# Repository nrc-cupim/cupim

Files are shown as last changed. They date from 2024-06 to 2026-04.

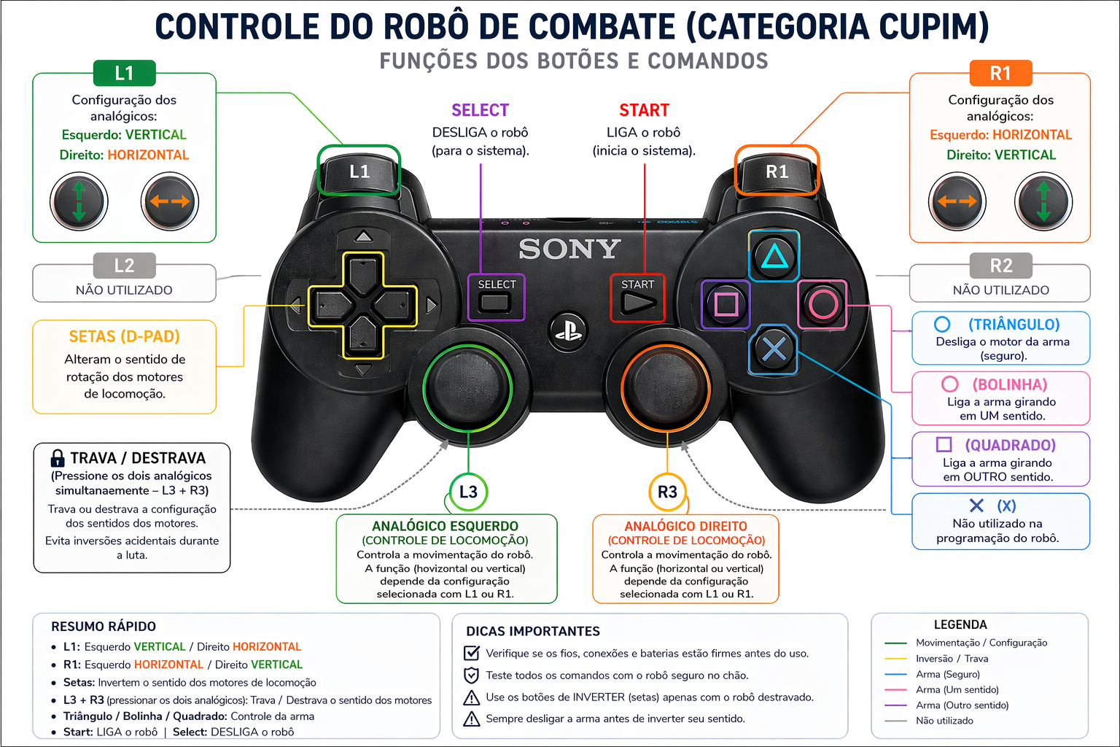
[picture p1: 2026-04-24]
Codigos/funcoes-controle.png

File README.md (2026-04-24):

# start\_Engenharia Automação e Elétrica

Materiais desenvolvidos para a atividade.

* Apostilas: contém documentação completa sobre a eletrônica (hardware) e a programação (firmware) do robô, além de tutoriais de instalação das ferramentas necessárias (drivers, softwares, bibliotecas, etc)
  
* Códigos: contém o código principal do robô, código para aplicar o filtro MAC do controle e código para descobrir os parâmetros de um controle
  
* Hardware: contém fotos da placa, arquivo para produção/prototipagem (GERBER) e os arquivos de projeto (abrir no software EasyEDA)
  
* Mecânica: contém arquivos dxf (para corte a laser) das peças da estrutura mecânica dos robôs desse ano e dos anos anteriores e modelos de rodas alternativas

----

## Regras

Para acessar as regras da categoria de cupim e os critérios de julgamento das lutas, clique [aqui](https://events.robocore.net/ironcup-2026/rules)

----

## Vídeos
* [IronCup 2026 - 10 Anos](https://www.youtube.com/watch?v=BdECDlp-MfM)
* [Finais start_Inatel 2025](https://www.youtube.com/watch?v=BfLkFSdPqyA)

----

## Links uteis

* [Biblioteca Bluepad32](https://bluepad32.readthedocs.io/en/latest/)
* [Tutorial filtro MAC do controle](https://bluepad32.readthedocs.io/en/latest/FAQ/#how-to-pair-just-one-controller-to-one-particular-board)
* [Driver ESP32](https://www.silabs.com/developers/usb-to-uart-bridge-vcp-drivers)
* [IDE Arduino](https://www.arduino.cc/en/software)
* [Onshape](https://www.onshape.com/en/)
* [EasyEDA](https://easyeda.com/pt)
* [Manual ponte H DRV8833](https://www.ti.com/lit/ds/symlink/drv8833.pdf?ts=1716022162879)

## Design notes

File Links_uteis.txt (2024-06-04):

Bilioteca controle:	https://bluepad32.readthedocs.io/en/latest/
			https://github.com/ricardoquesada/bluepad32

Tutorial filtro MAC controle: https://bluepad32.readthedocs.io/en/latest/FAQ/#how-to-pair-just-one-controller-to-one-particular-board

Driver ESP32: https://www.silabs.com/developers/usb-to-uart-bridge-vcp-drivers

Arduino: https://www.arduino.cc/en/software

OnShape: https://www.onshape.com/en/

Easy EDA: https://easyeda.com/pt

Datasheet ponte H: https://www.ti.com/lit/ds/symlink/drv8833.pdf?ts=1716022162879

Datasheet TIP 122: https://www.st.com/resource/en/datasheet/tip120.pdf

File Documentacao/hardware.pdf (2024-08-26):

# Guia de hardware

## Sumário

1 Componentes | 3
2 Esquema elétrico | 14

## 1 Componentes

### 1.1 Célula de bateria

Responsável por alimentar o robô, permitindo seu funcionamento. A bateria utilizada neste projeto é do tipo Li-ion 18650.

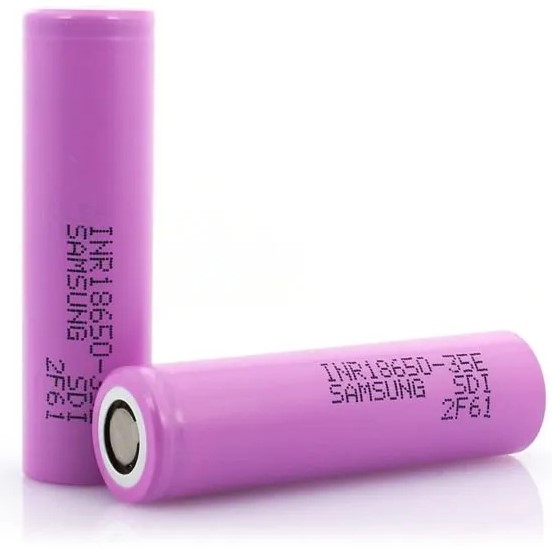
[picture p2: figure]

Figure 1: Célula de bateria 18650

- Capacidade: 2200mAh (quanto maior a capacidade, mais tempo a bateria irá durar);
- Polaridade: cada bateria possui um lado positivo e um lado negativo. O lado da bateria que possui um chanfro / corte / ressalto é o positivo. E possível ainda identificar a ´ polaridade utilizando um multímetro;
- Tensão Nominal: A tensão nominal de uma célula 18650 é de 3.7V, podendo variar entre 4.2V (quando completamente carregada) e 3.2V (quando descarregada).

E possível associar células de baterias em série (positivo de uma conectada no negativo de outra) ´ para produzir tensões maiores. Ao associá-las dessa forma, a tensão de saída será igual ao somatório das tensões de cada célula de bateria.

Existem modelos de baterias com diferentes capacidades, tamanhos, pesos e tipos de materiais. Existem ainda baterias que já vêm com várias células associadas (2s, 3s, ...).

### 1.2 Suporte de bateria

Componente utilizado para manter as baterias firmemente no lugar, garantindo uma conexão elétrica segura e estável entre as baterias e o circuito. Esse suporte permite a conexão de duas baterias Li-íon 18650 em série.

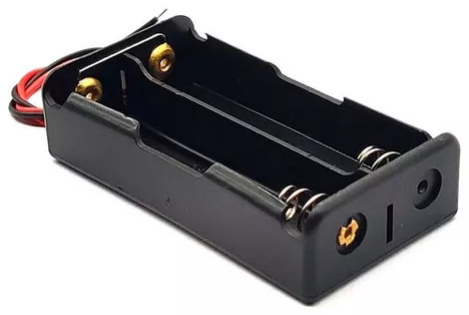
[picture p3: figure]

Figure 2: Suporte para 2 baterias 18650

- No interior do suporte há um desenho mostrando como cada bateria deve ser colocada;
- Polaridade da saída: o fio vermelho é o positivo (+) e o fio preto, o negativo (-).

### 1.3 Carregador de bateria

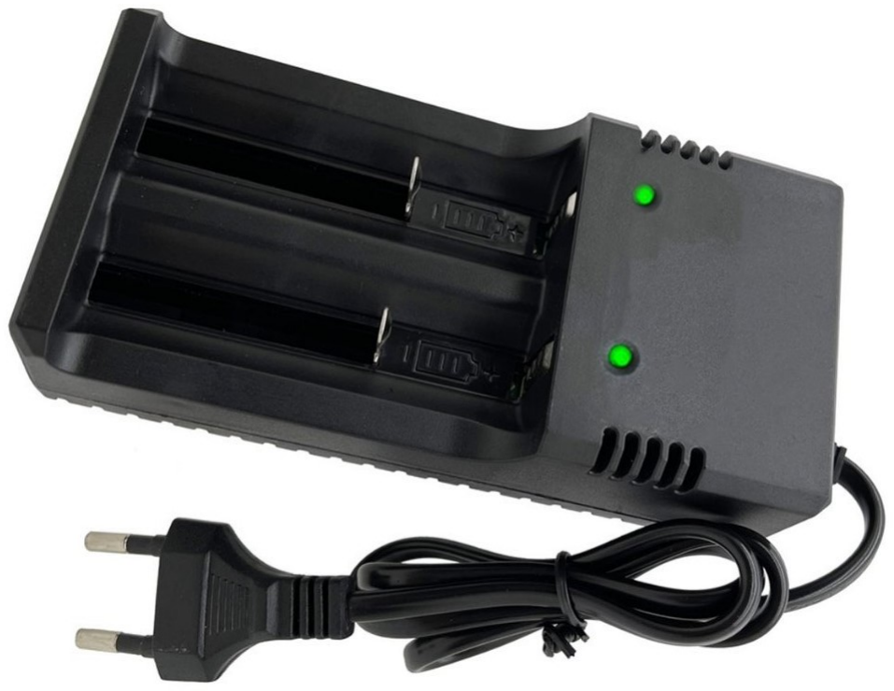
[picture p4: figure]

Figure 3: Carregador para duas baterias 18650

Para carregar a bateria, basta encaixa-la no interior do suporte, pressionando a parte metálica que fica no meio para baixo. O positivo da bateria deve ficar para cima (conector mais próximo ao led de indicação).

- Led vermelho: indica que a bateria não está completamente carregada;
- Led verde: indica que a bateria está completamente carregada.

Observação: é necessário conectar o carregador na tomada para que os leds indiquem corretamente o estado da bateria.

### 1.4 Regulador 7805

Utilizado para regular a tensão da bateria, que varia de 6,4 a 8,4 V, para 5 V. Essa regulagem é necessária para se fazer a alimentação da ESP32.

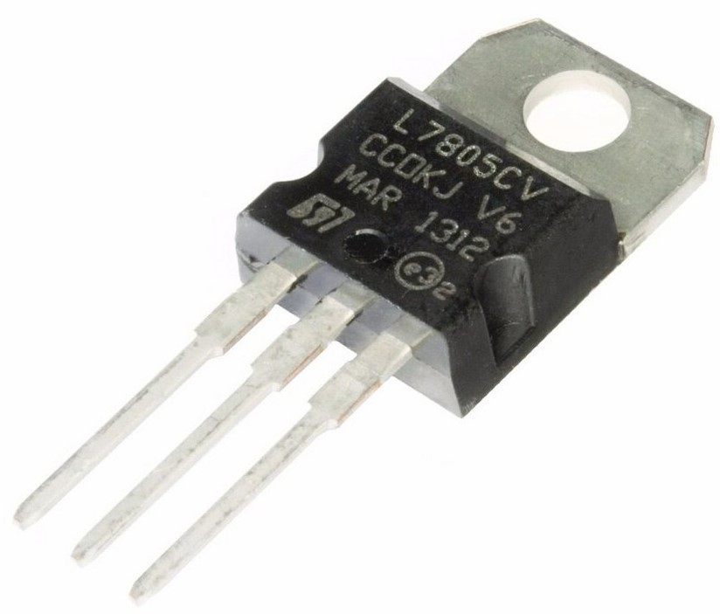
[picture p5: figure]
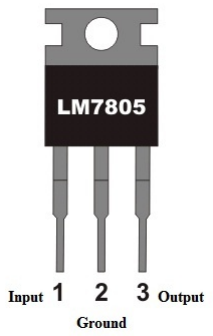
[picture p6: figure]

(a) (b)

Figure 4: Regulador 7805

- Pinagem: possui três terminais - entrada (Vin), terra (GND) e saída (Vout).
- Parâmetros elétricos:

– Tensão de entrada: 7,5 a 35V
– Tensão de saída: 5V
– Maxima corrente que o componente é capaz de fornecer na saída: 1A

Observações:

- Para mais informações do componente, consulte seu datasheet
- Caso a conexão dos pinos não seja feita da forma correta, o componente explode. Portanto, deve-se tomar muito cuidado ao fazer as conexões.
- E recomendado a utilização de um dissipador de calor para impedir que o componente ´ esquente muito. Entretanto, este não foi utilizado devido à limitação de espaço na placa.

### 1.5 ESP32 WROOM-32

Microcontrolador responsável por ler as informações do controle Bluetooth e atuar no controle dos motores. E o cérebro do robô. ´

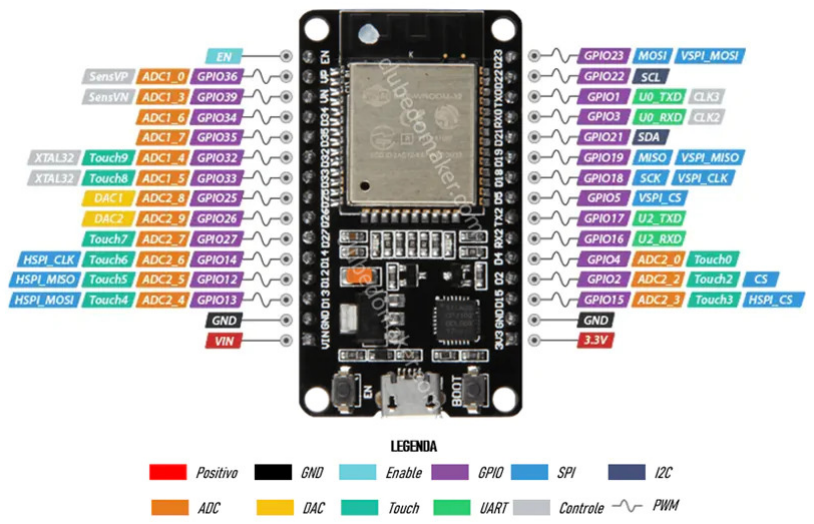
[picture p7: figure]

Figure 5: Pinagem ESP32 WROOM32 30 pinos

A alimentação da placa pode ser feita por meio do conector USB presente na placa ou então por meio do pino VIN. A tensão recebida no pino VIN deve ser de 5V. As opções de alimentação são mutuamente exclusivas, ou seja, nunca se deve alimentar a placa das duas maneiras simultaneamente. Se for alimentar pelo pino VIN, deve-se remover o cabo USB e vice-versa. No projeto desenvolvido, a tensão vinda da bateria é regulada para 5V e é encaminhada para o pino VIN da ESP.

O controlador trabalha em nível lógico 3,3V. Portanto, todo sinal de saída da placa poderá ter até 3,3V e todo sinal de entrada deve ter até 3,3V.

Do lado oposto ao conector USB fica a antena Bluetooth do microcontrolador. A fim de evitar problemas de conexão (queda de conexão e lentidão) entre a placa e o controle, deve-se manter a antena o mais longe possível de fios de energia e motores, pois estes são fontes de interferências eletromagnéticas.

Com base no diagrama, percebe-se que cada pino possui diversas funcionalidades. Entretanto, utilizaremos apenas as funcionalidades GPIO e PWM. GPIO indica que o pino pode operar como entrada e saída digital, mandando / recebendo 0V ou 3,3V apenas. Já PWM indica que o pino é capaz de gerar um sinal PWM de saída, ou seja, o pino é capaz de gerar valores de tensão de 0V a 3,3V, não apenas 0V ou 3,3V.

Observação: apesar de estarem identificados como GPIO, os pinos D34, D35, D36 e D39 não funcionam como saída digital, funcionam apenas como entrada.

### 1.6 Motor DC 130

Componente capaz de exercer uma força rotativa. Constituido internamente de um par de ímãs (estator - parte fixa) e um núcleo (rotor - parte móvel).

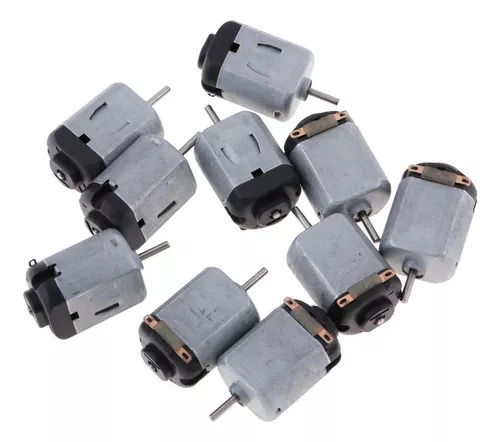
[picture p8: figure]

Figure 6: Motor DC 130

- Tensão de Operação: de 3 a 6V.
- Alimentação: feita por meio dos terminais de cobre externos. Coloca-se o positivo da fonte de alimentação em um terminal e o negativo em outro.

Observações:

- E possível trabalhar com níveis de tensão maiores nos motores (overvoltage), produzindo ´ uma maior rotação. Entretanto, isso pode danificar o componente. ;
- A direção da rotação (horária e anti-horária) pode ser invertida invertendo a alimentação (trocar o positivo e negativo de terminal);
- Os parâmetros de tensão do motor podem mudar em função de sua construção mecânica (tamanho do núcleo, força do ímã, etc).

### 1.7 Motor DC 130 com redução

Motor DC 130 que incorpora um sistema de engrenagens para converter a rotação do motor em força (torque). O motor por si só não possui força suficiente para movimentar o robô, por isso a caixa de redução é utilizada. A relação de conversão velocidade / torque depende da relação de engrenagens da caixa de redução.

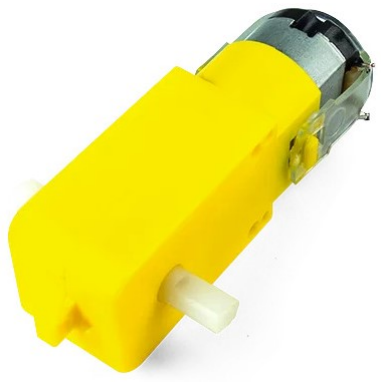
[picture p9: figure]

Figure 7: Motor DC 130 com redução

### 1.8 Transistor TIP122

Transistores são comumente utilizados como interruptores eletrônicos em circuitos elétricos, controlando o acionamento de cargas. Em nosso caso, iremos utilizar um transistor modelo TIP122 para ligar e desligar o motor da arma.

- Pinagem: possui 3 terminais, base, coletor e emissor.
- Funcionamento: quando desenergizado, não há conexão interna entre o coletor e o emissor. Ao energizar a base, uma conexão interna entre o coletor e o emissor é estabelecida.
- Parâmetros elétricos:

– Máxima corrente que pode passar pelo componente [Ic]: 5A
– Máxima tensão que componente pode estar submetido [Vce]: 100V – Ganho mínimo [hfe]: 1000

Observações:

- Para mais informações sobre o componente, consulte o datasheet;
- Para escolher o modelo de transistor a ser utilizado em um projeto, deve-se levar em consideração a tensão e a corrente demandada pela carga a ser controlada.

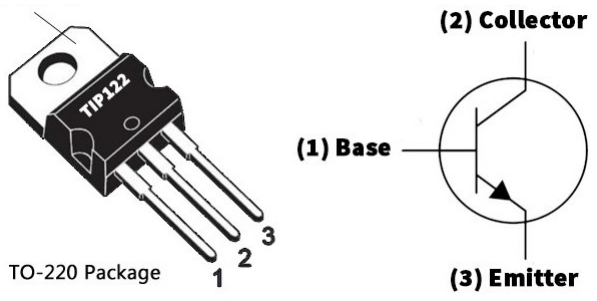
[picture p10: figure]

Figure 8: TIP 122

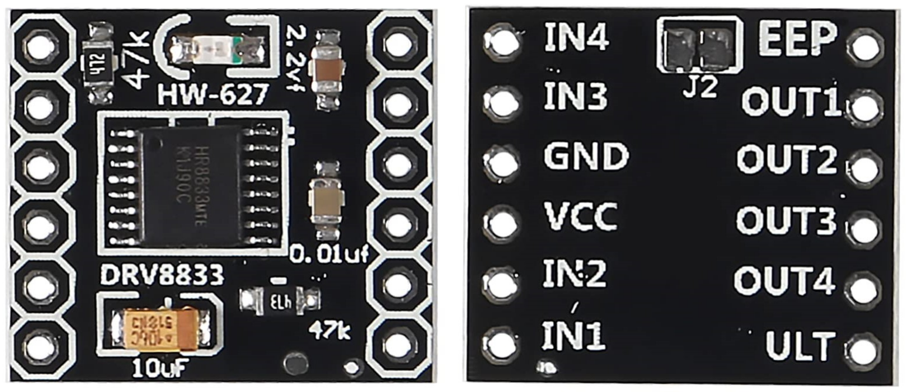
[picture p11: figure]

Figure 9: Ponte H DRV8833

### 1.9 Ponte H DRV8833

Componente utilizado para fazer o controle de velocidade e sentido de rotação dos motores de locomoção (motor com caixa de redução).
Características:
- Quantidade de canais (motores): 2
- Tensão de alimentação: 2,7 a 10,8V
- Máxima corrente que cada canal consegue fornecer continuamente: 1,4A
- Máxima tensão aceita pelos pinos de controle: 7V

O sentido e a velocidade de rotação de cada motor são controlados via um par de pinos de entrada (IN). Um dos pinos do par recebe GND e o outro, Vcc. O sentido de rotação muda em função de qual pino receber o Vcc e qual receber o GND. Cada canal possui também 2 pinos de saída, por onde é feita a alimentação do motor.

Para controlar a velocidade de rotação, deve-se utilizar uma técnica chamada PWM, que permite gerar valores de tensão entre 0 e 3,3V (Vcc) na saída da ESP32, variando assim a velocidade.

Pinagem:

- IN1 e IN2: pinos de controle do canal 1;
- OUT1 e OUT2: pinos de saída do canal 1;
- IN3 e IN4: pinos de controle do canal 2;
- OUT1 e OUT2: pinos de saída do canal 2;
- VCC e GND: pinos de alimentação da ponte H e dos motores;
- ULT e EEP: não utilizados.

Observações:

- O pino de GND da ponte H e do ESP32 devem ser interconectados. Isso é necessário para que a ponte H consiga interpretar corretamente a tensão recebida pelos pinos de controle (IN);
- Para mais informações sobre o componente, consulte o datasheet.

### 1.10 Chave Liga/Desliga

Utilizada para ligar e desligar o robô.

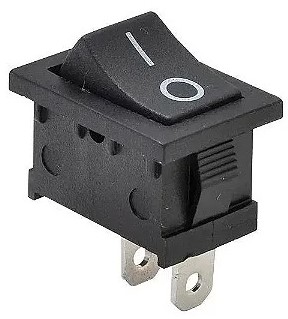
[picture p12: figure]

Figure 10: Chave tipo gangorra Liga/Desliga

Funcionamento: ao pressionar a chave para um dos lados, fecha-se o contato mecânico entre o pino central (chamado de comum) e o pino lateral (referente ao lado em que o botão foi pressionado).

### 1.11 LED

Utilizado para indicar o estado do robô: ligado (led aceso) e desligado (led apagado).

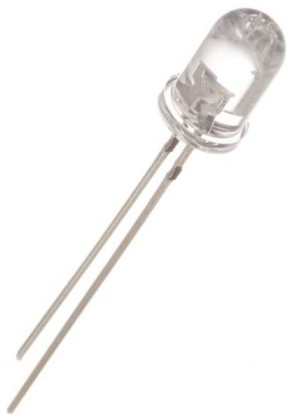
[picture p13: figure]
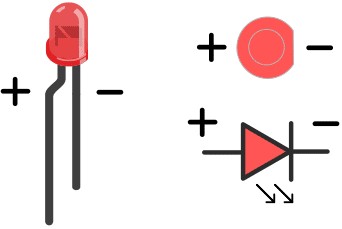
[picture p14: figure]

(a) (b)

Figure 11: LED

E um componente que possui polaridade, ou seja, um terminal deve receber especificamente o Vcc ´ e o outro, o GND. Observando o interior do componente, percebe-se que existem duas placas. A placa maior indica o terminal negativo.

O led utilizado no robô é da cor azul, diâmetro de 5mm e é do tipo alto brilho. Para esse tipo de componente, temos os seguintes parâmetros elétricos:

- Tensão necessária para funcionamento: 2,5 a 3V
- Máxima corrente que pode passar pelo componente: 20mA

### 1.12 Capacitor

Capacitores são componentes eletrônicos que armazenam e liberam energia elétrica. Pense neles como baterias bem pequenas. Possuem uma ampla gama de aplicações, mas em nosso projeto estão sendo utilizados para filtragem e desacoplamento.

Filtragem e desacoplamento: os capacitores de desacoplamento funcionam como fones de ouvido com cancelamento de ruído. Eles ajudam a ”limpar” esses ruídos indesejados do circuito, permitindo que os componentes funcionem corretamente.

Parâmetros elétricos: os parâmetros elétricos mais importantes de um capacitor são a sua máxima tensão de operação, que indica com até quantos volts ele pode ser alimentado, e sua capacidade de armazenamento. A capacidade de armazenamento (capacitância) normalmente é dada em Farad (F) e quanto maior, mais energia o componente consegue armazenar.

Podem ser de diversos tipos de materiais, como, por exemplo: poliéster, cerâmica e eletrolítico.

### 1.12.1 Capacitor de cerâmica:

Não possuem polaridade de conexão. Geralmente suportam tensões relativamente altas e possuem baixa / média capacidade de armazenamento.

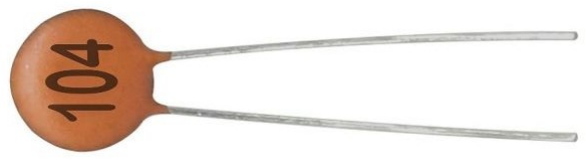
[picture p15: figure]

Figure 12: Capacitor de cerâmica

### 1.12.2 Capacitor eletrolítico:

Conhecidos por sua alta capacitância e capacidade de armazenamento de energia. São polarizados, o que significa que possuem um terminal positivo (ânodo) e um terminal negativo (cátodo). A conexão incorreta pode danificar o capacitor ou o circuito.

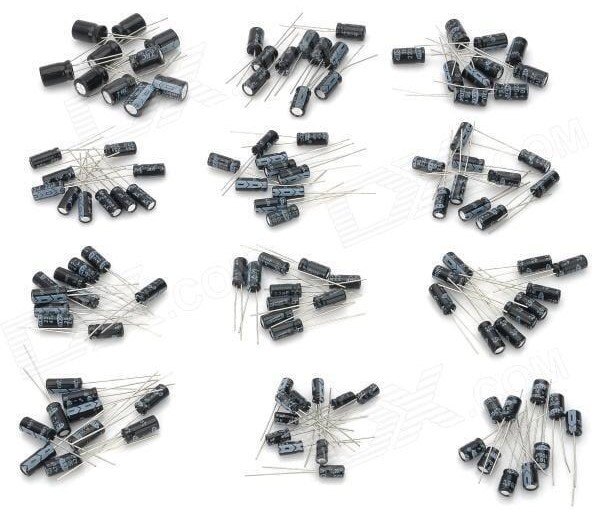
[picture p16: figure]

Figure 13: Capacitor eletrolítico

### 1.13 Resistor

São componentes eletrônicos que limitam o fluxo de corrente elétrica em um circuito. Eles são caracterizados pela sua resistência elétrica, medida em ohms (Ω).

Observação: além de possuir a resistência necessária para o projeto, o resistor deve ser capaz de suportar a potência (tensão x corrente no componente) que será dissipada nele.

- Resistor de 330Ω (à esquerda): utilizado para limitar a tensão e a corrente recebidas pelo led, de modo a evitar que ele seja danificado;
- Resistor de 4,7kΩ (à direita): utilizado para fazer o correto acionamento do transistor TIP 122, permitindo que a arma seja ligada e desligada.

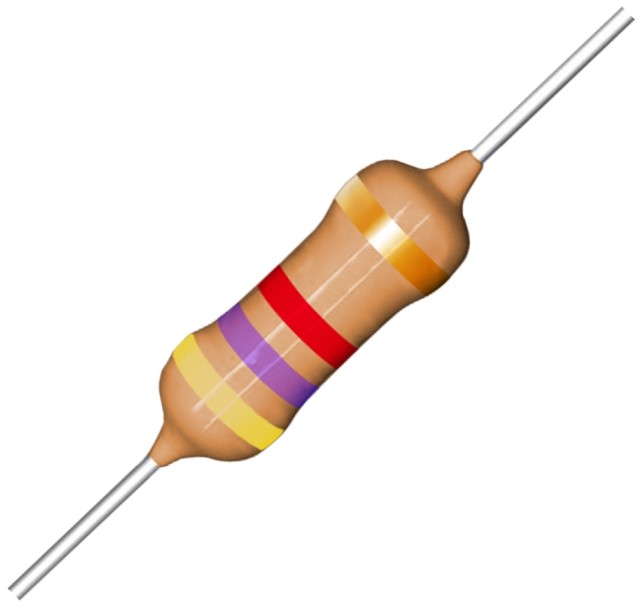
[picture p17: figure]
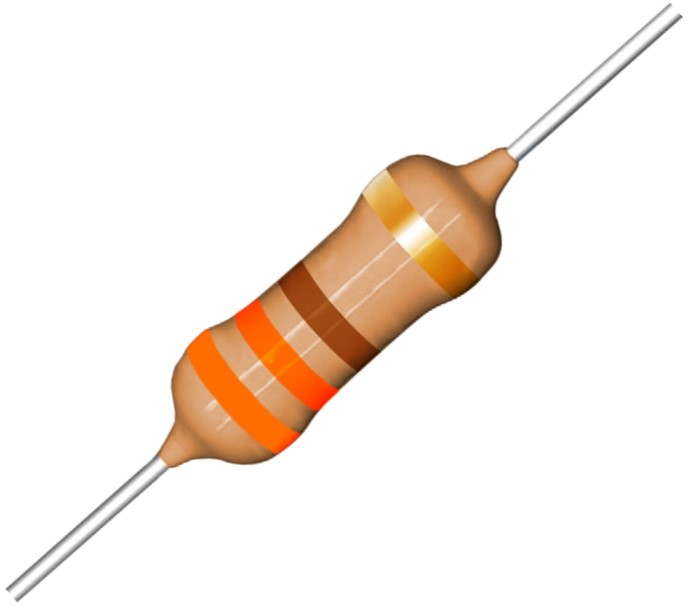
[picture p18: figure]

(a) (b)

Figure 14: Resistores

## 2 Esquema elétrico

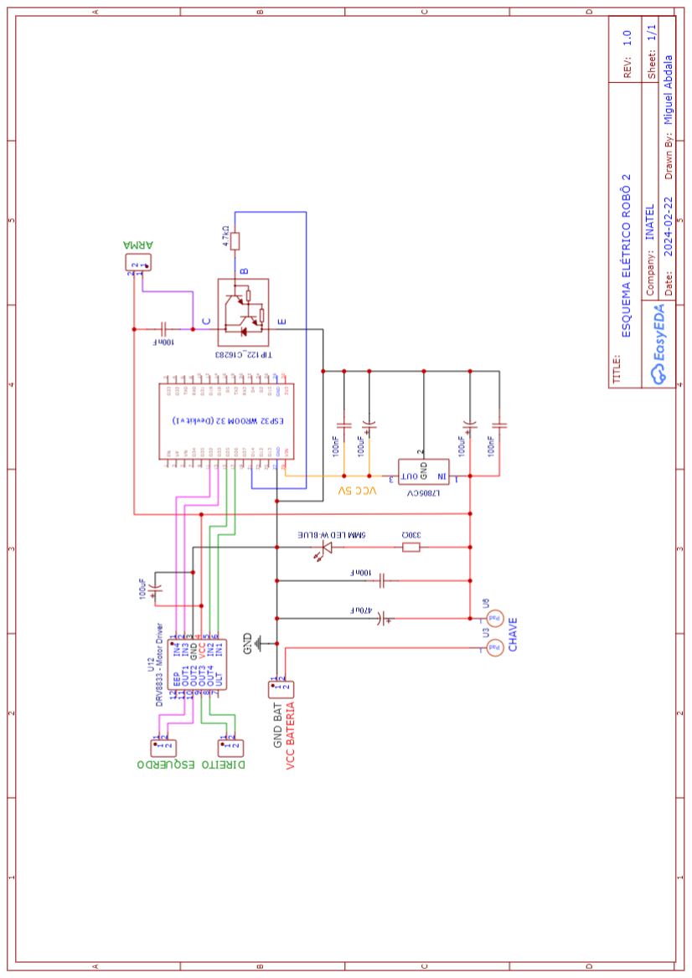
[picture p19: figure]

Figure 15: Esquema elétrico robô 2

O esquema elétrico do robô 1 e do robô 2 são extrememente semelhantes. A única diferença é que, no caso do robô 1, a base do transistor está conectada ao pino D27 da ESP32.

### 2.1 Alimentação da placa

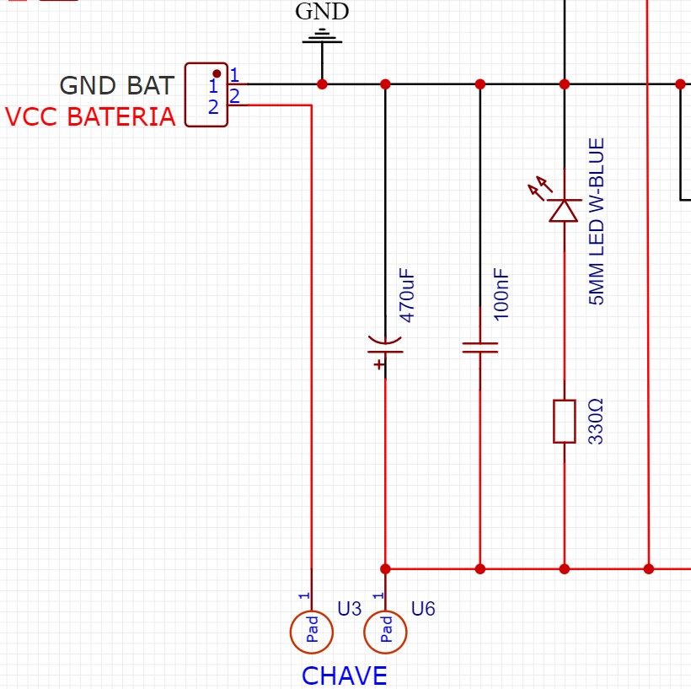
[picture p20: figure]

Figure 16: Entrada de energia da placa

Nessa parte do circuito podemos observar o conector de entrada da bateria, por onde a energia para alimentar a placa entra, a chave liga e desliga do sistema e o led de indicação de funcionamento. Ao pressionar a chave, a conexão entre o Vcc da bateria e o resto do circuito é estabelecida, energizando o robô. Nessa parte primária de alimentação temos 2 capacitores, um de cerâmica, com valor de 100nF e um eletrolítico (polarizado), com valor de 470uF.

### 2.2 Alimentação da ESP32

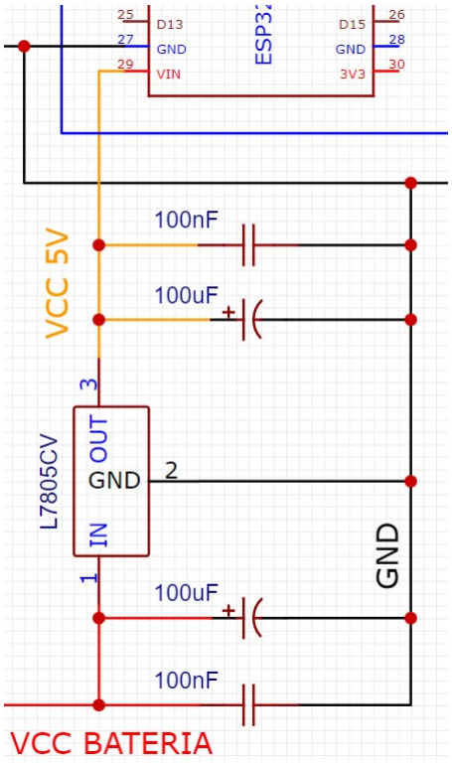
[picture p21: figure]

Figure 17: Alimentação da ESP32

A energia proveniente da bateria alimenta o regulador de tensão. Este por sua vez alimenta a ESP32. Tanto na entrada quanto na saída do regulador um par de capacitores está sendo utilizado para filtrar o sinal. Cada par é composto por um capacitor de cerâmica de 100nF e um capacitor eletrolítico, de 100uF.

### 2.3 Controle de movimentação

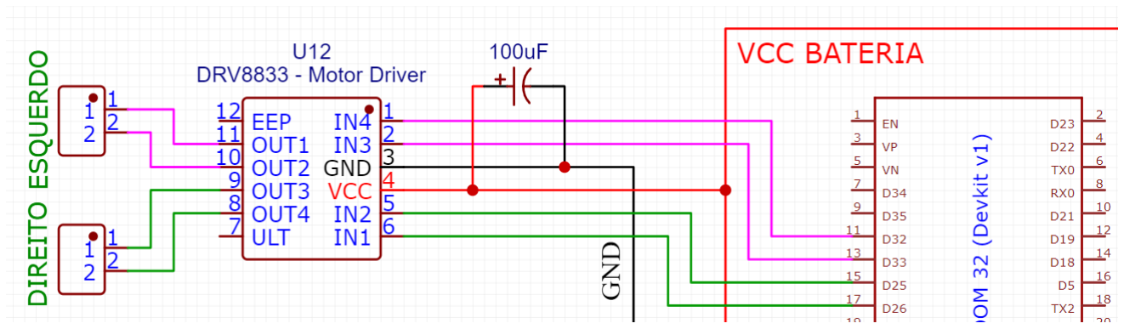
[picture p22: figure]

Figure 18: Conexões da ponte H DRV8833

Conforme comentado no tópico 1., cada canal da ponte H possui 2 pinos de comando, que controlam o sentido e a velocidade de rotação do motor. O canal 1 é controlado pelos pinos D26 e D25, enquanto o canal 2 é contrlado por D33 e D32. Observando a pinagem da ESP32 apresentada no tópico 1., percebe-se que todos esse pinos possuem a funcionalidade PWM. Os pinos de saída de cada canal estão conectados aos terminais de um conector, onde o motor é fixado.

A alimentação do DRV883 é feita diretamente pela bateria. Portanto, a tensão recebida pelos motores é proporcional (depende do sinal PWM de controle) a tensão da bateria. Devido á isso, quanto maior a tensão de alimentação, mais rápido os motores irão girar. Em paralelo á alimentação da ponte H à um capacitor eletrolítico de 100uF, utilizado para filtragem do sinal de aliemntação.

### 2.4 Acionamento da arma

Conforme comentado no tópico 1., o acionamento da arma é feito utilizando um transistor Tip122. Percebe-se que a base, pino responsável por disparar a condução entre coletor e emissor, está conectada a um pino da ESP32, que está configurado como saída. Dessa forma, sempre que o pino estiver acionado (nível lógico 1 / HIGH), o Tip irá conduzi e o motor da arma irá ligar. Foi necessário utilizar um resistor na base do transistor para garantir que ele receba os valores de tensão e corrente ideiais para se fazer o acionamento.

Um terminal do conector onde o motor é acomplado está conectado diretamente à bateria. Já o outro terminal está em aberto. Energizando o pino da ESP32, o GND que está no emissor irá ”aparecer” no coletor (curto interno), fazendo com que o motor rotacione. O capacitor em paralelo com o conector serve apenas como filtro.
Para adicionar mais motores na arma, basta replicar o circuito, utilizando outro pino da ESP32. É necessário adicionar também algumas linhas de código para ligar o pino que controla o motor.

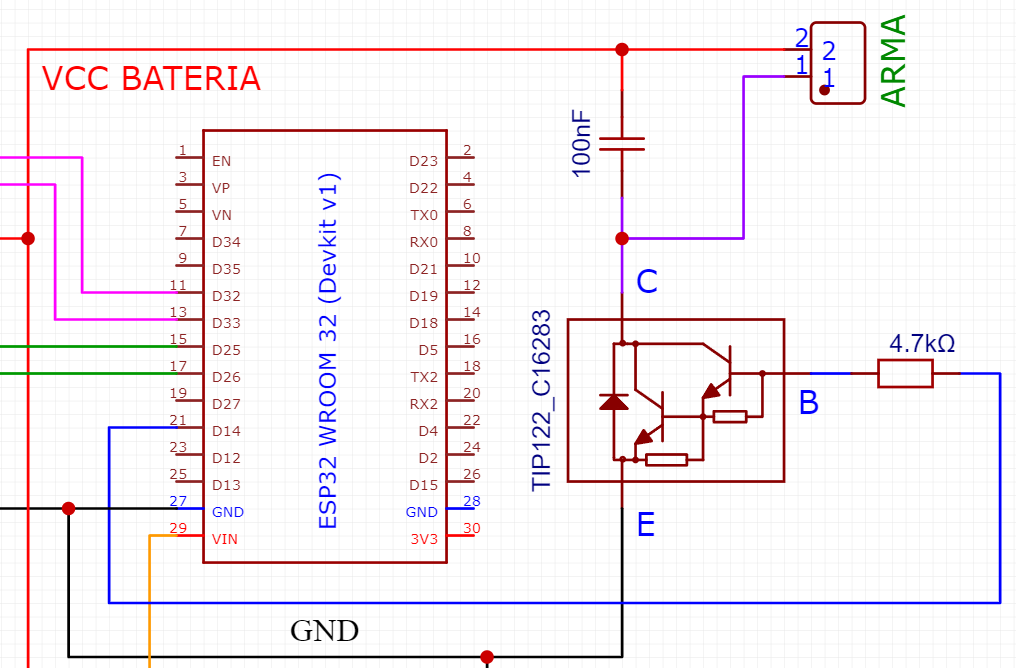
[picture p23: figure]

Figure 19: Circuito de acionamento da arma

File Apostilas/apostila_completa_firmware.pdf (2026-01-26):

# Apostila de Firmware

### Miguel Abdala

2026

## Conteúdo

## 1 Instalações

### 1.1 Arduino IDE

A IDE (Integrated Development Environment) Arduino é um software que proporciona um ambiente de desenvolvimento completo para programar microcontroladores Arduino,
ESP32, entre outros. E onde se escreve, edita, compila e carrega códigos ( ´ | sketches) para
o robô. Para fazer o download e a instalação do aplicativo, siga as instruções abaixo:
1. Acesse a página de download da IDE Arduino, clicando aqui; (https://www.arduino.cc/en/software)
2. Selecione o sistema operacional utilizado pelo seu computador. Para computadores Windows, selecione a primeira opção, conforme demonstrado na Figura 1 abaixo;

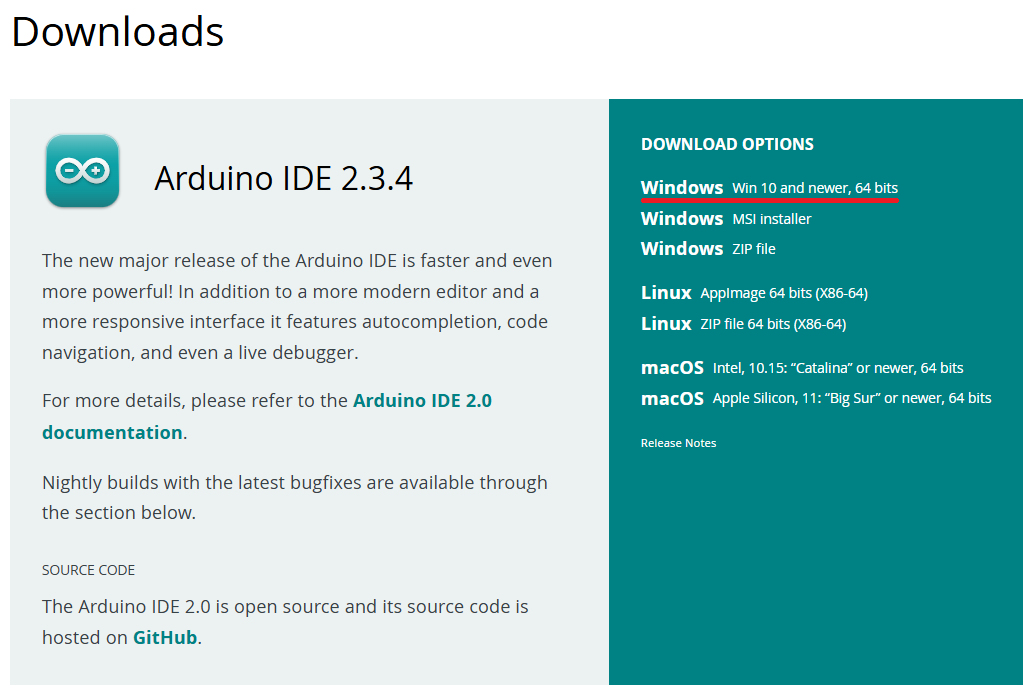
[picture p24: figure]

Figura 1: Página de seleção do sistema operacional

3. Na página para a qual você foi redirecionado, selecione a opção JUST DOWNLOAD. Você será redirecionado para outra página;

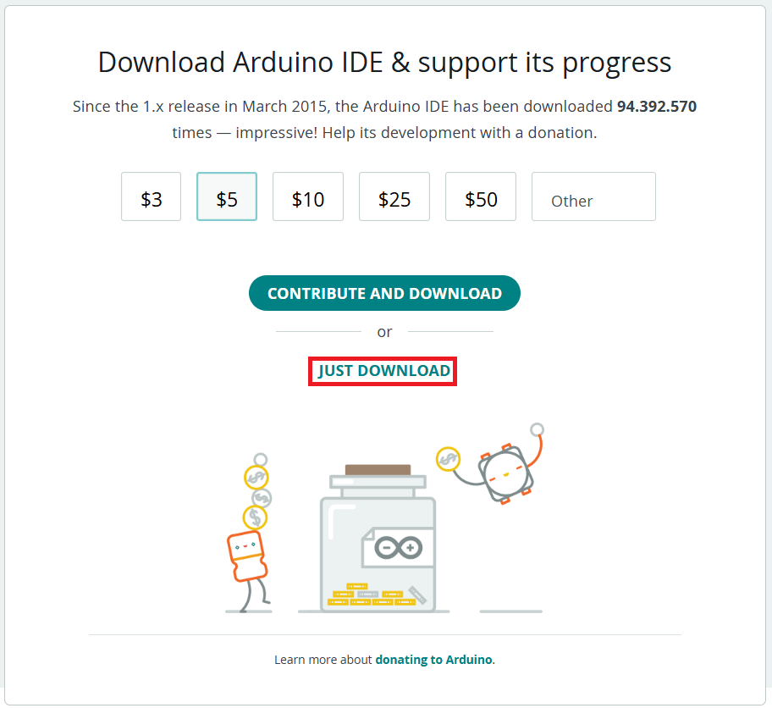
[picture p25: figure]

Figura 2: Página Just Download 1

4. Selecione novamente a opção JUST DOWNLOAD. Feito isso, o arquivo será baixado;


Figura 3: Página Just Download 2

5. Acesse a pasta onde o arquivo baixado foi salvo e dê um duplo clique nele para executá-lo;

6. Na janela que abrir, clique em Eu Concordo, para concordar com os Termos de Licença do programa;

Figura 4: Concordância com os Termos de Licença

7. Selecione para quais usuários de seu computador o aplicativo deve ser instalado. Recomenda-se instalar apenas para seu usuário. Feita a seleção. Clique em Próximo;

Figura 5: Opções de instalação


8. Escolha o local de instalação do programa. Recomenda-se deixar a Pasta de Destino padrão escolhida pelo próprio instalador. Clique em Instalar;

Figura 6: Seleção do Local de Instalação do programa

9. Finalizada a instalação, clique em Concluir. A IDE Arduino abrirá logo em sequência.

Figura 7: Concluindo instalação

### 1.2 Driver CP210x

O driver especifica para o computador a forma correta de se fazer a comunicação com a ESP32, permitindo o correto carregamento do código do robô no microcontrolador. Caso não seja instalado, o computador não irá reconhecer a ESP32 ao conectá-la via USB. O driver a ser instalado é o CP210x. As instruções abaixo demonstram como fazer a instalação:

1. Acesse a página de download, clicando aqui; (https://www.silabs.com/developer-tools/usb-to-uart-bridge-vcp-drivers?tab=downloads)
2. Selecione o sistema operacional utilizado pelo seu computador. Para computadores Windows, selecione a primeira opção, conforme demonstrado na Figura 8 abaixo. Ao clicar em uma das opções, você será redirecionado para outra página;


Figura 8: Download do driver ESP32

3. Abra a pasta onde o arquivo foi salvo. O arquivo baixado está no formato .zip. E necessário extraí-lo antes de prosseguir. Para tal, clique sobre ele com o botão ´ direito do mouse e depois clique em extrair;
4. Abra a pasta originada a partir da extração do arquivo .zip, clique no arquivo de nome silabser com o botão direito e clique em instalar;
5. Na janela que aparecer, clique em Abrir. Caso uma janela de notificação do Windows abra logo em sequência, pressione Sim. Feito isso, o driver estará instalado;
6. Clique em Ok para finalizar o processo.

Figura 9: Iniciando instalação do driver

Figura 10: Instalando driver

Figura 11: Driver instalado com sucesso

### 1.3 Bibioteca Bluepad32

Bibliotecas, no contexto de programação, são conjuntos de códigos prontos que facilitam a criação de projetos, evitando que o programador precise escrever tudo do zero. Por exemplo, se você quiser usar um sensor de temperatura, pode instalar uma biblioteca específica que já contém os comandos necessários para fazer o sensor funcionar, economizando tempo. Nesta aplicação, iremos utilizar a biblioteca Bluepad32 para fazer a conexão da ESP32 com o controle Bluetooth.

O passo a passo abaixo demonstra como fazer a instalação da biblioteca. Ele foi feito com base na documentação original, disponível no site da biblioteca (tópico Arduino + ESP32 board - Option A). Clique aqui (https://bluepad32.readthedocs.io/en/latest/) para acessar a documentação original.

1. Abra a IDE Arduino. No canto superior esquerdo, clique em File (Arquivo) e selecione a opção Preferences (Preferências);


Figura 12: Abrindo campo de Preferências da IDE

2. Na janela que abrir, selecione a opção Settings (Configurações). Depois, clique no botão identificado na Figura 13 abaixo;


Figura 13: Janela de Preferências

3. Cole os links abaixo no campo que aparecer, um embaixo do outro. Esses links indicam à IDE Arduino onde procurar os arquivos da biblioteca no momento em que a instalação for solicitada;

https://raw.githubusercontent.com/espressif/arduino-esp32/gh-pages/package_esp32_index.json (https://raw.githubusercontent.com/espressif/arduino-esp32/gh-pages/package_esp32_index.json)

https://raw.githubusercontent.com/ricardoquesada/esp32-arduino-lib-builder/master/bluepad32_files/package_esp32_bluepad32_index.json (https://raw.githubusercontent.com/ricardoquesada/esp32-arduino-lib-builder/master/bluepad32_files/package_esp32_bluepad32_index.json)


Figura 14: Identificação dos locais de download da biblioteca

4. Novamente na barra superior, selecione agora a opção Tools (Ferramentas). Clique na opção Board (Placa) e depois em Board Manager (Gerenciador de Placas);

Figura 15: Abrindo o gerenciador de placas

5. Pesquise por ESP32 e instale as bibliotecas esp32 e esp32 bluepad32. Instale uma biblioteca de cada vez, caso contrário, erros podem acontecer durante a instalação;


Figura 16: Instalando placas

Observações:
- A biblioteca Bluepad32 utiliza a biblioteca esp32 como base; por isso, ambas devem ser instaladas;
- As bibliotecas já estavam instaladas; por isso, aparece o REMOVE (Remover) na Figura 16 ao invés de INSTALL (Instalar);

- A instalação da biblioteca Bluepad32 é diferente da instalação da grande maioria das bibliotecas ”Arduino”. Ela é instalada como placa ao invés de biblioteca propriamente dita.

## 2 Linguagem Arduino

A linguagem de programação utilizada para programar a ESP32 foi a linguagem nativa da plataforma Arduino. Nos links abaixo, é possível encontrar um tutorial completo explicando todas as funcionalidades da linguagem, juntamente com exemplos de implementação.

- Variáveis (clique aqui para ir à página) (https://docs.arduino.cc/language-reference/pt/#vari%C3%A1veis)
- Estruturas (clique aqui para ir à página) (https://docs.arduino.cc/language-reference/pt/#estruturas)
- Funções (clique aqui para ir à página) (https://docs.arduino.cc/language-reference/pt/#fun%C3%A7%C3%B5es)

Para entender melhor o código do robô, recomenda-se o seguinte roteiro de estudos:

1. Estruturas - Sketch
2. Variáveis - Tipos de Dados
3. Estruturas - Operadores Aritméticos
4. Estruturas - Outros Elementos da Sintaxe
5. Estruturas - Estruturas de Controle - IF/ELSE
6. Estruturas - Operadores de Comparação
7. Estruturas - Operadores Booleanos
8. Funções - Entradas e Saídas Digitais
9. Variáveis - Constantes
10. Funções - Entradas e Saídas Analógicas
11. Funções - Funções Matemáticas

## 3 Código principal do robô

### 3.1 Importando Bibliotecas

Nas duas primeiras linhas do programa, há a inclusão da biblioteca utilizada para fazer a comunicação com o controle de PS3 (Bluepad32) e a inclusão do arquivo de configurações. O arquivo de configurações será explicado posteriormente.

Figura 17: Importando biblioteca e arquivo de configurações

### 3.2 Definição de variáveis

Após as inclusões, oito variáveis utilizadas ao longo do programa são declaradas. Abaixo consta uma explicação sobre cada variável.

- myControllers: representa de forma lógica/virtual o controle bluetooth utilizado para controlar o robô;
- roboLigado: indicador do estado do robô ligado;

– ligado = verdadeiro / true

– desligado = falso / false

- configsTravadas: indica se as configurações dos joysticks e dos sentidos de rotação dos motores de locomoção estão travadas ou não;

– travada = verdadeiro / true

– destravada = falso / false

- sentidoMotorEsquerdo e velocidadeMotorEsquerdo: indicam os pinos nos quais os terminais do motor esquerdo do robô estão conectados;
- sentidoMotorDireito e velocidadeMotorDireito: indicam os pinos nos quais os terminais do motor direito do robô estão conectados;
- direitoVesquerdoH e direitoHesquerdoV: indicam a forma de pilotagem do robô;

– joystick direito funcionando na vertical e esquerdo, na horizontal

– joystick direito funcionando na horizontal e esquerdo, na vertical


Figura 18: Declaração de variáveis

### 3.3 Função desligaRobo()

Esta função contém todos os comandos necessários para interromper o funcionamento do robô. Nas primeiras linhas da função, utiliza-se o comando analogWrite (escrita analógica) para desligar (0) as saídas associadas ao controle dos motores de arma e de locomoção (todos os motores são configurados com velocidade 0). Ao final, define-se o estado do robô como desligado (roboLigado = false).

Figura 19: Função desligaRobo()

### 3.4 Função onConnectedController()

Estabelece a ligação virtual entre o controle e a ESP32. A execução da função é feita de forma automática pela ESP32 sempre que um controle é conectado. Caso deseje realizar alguma tarefa assim que o controle for conectado, basta adicionar o trecho de código no local indicado (entre o comentário e o comando break).


Figura 20: Função onConnectedController()

### 3.5 Função onDisconnectedController()

Rompe a ligação virtual entre o controle e a ESP32. A execução da função é feita de forma automática pela ESP32 sempre que um controle é desconectado. Caso deseje realizar alguma tarefa assim que o controle for desconectado, basta adicionar o trecho de código no local indicado (entre o comentário e o comando break).


Figura 21: Função onDisconnectedController()

Tanto a função onConnectedController() quanto a função onDisconnectedController() são definidas pela própria Bluepad32. Entretanto, algumas modificações foram feitas a fim de deixá-las mais simples e compactas.

Uma chamada da função desligaRobo() foi adicionada à função de desconexão do controle para garantir que o robô pare sua movimentação e armas em caso de perda de conexão com o controle (sistema de proteção exigido nas regras de competição da categoria cupim - fail safe).

### 3.6 Função processControllers()

Responsável por mapear o que foi pressionado no controle e, a partir disso, determinar e controlar o funcionamento dos motores de arma e locomoção. Toda a lógica de funcionamento do robô está descrita dentro desta função.

### 3.6.1 Verificação de conexão

A primeira tarefa realizada pela função é confirmar se há um dispositivo bluetooth conectado, se este está enviando dados e se ele é de fato um controle (Gamepad). Essa última verificação é feita pois a mesma biblioteca pode ser utilizada para a conexão com diversos tipos de dispositivos bluetooth (mouse, teclado, ...). Todos os trechos de código (processamento das informações do controle) após essa condição são executados apenas se ela for verdadeira.


Figura 22: Verificação de conexão

### 3.6.2 Liga/Desliga robô

Feita a verificação da conexão, verifica-se o estado dos botões Select e Start. Se Select for pressionado (miscSelect() retorna true / verdadeiro), o robô é desligado (roboLigado = false). Já se Start for pressionado (miscStart() retorna true / verdadeiro), o robô é ligado (roboLigado = true).

O controle dos motores de locomoção e de arma só funciona se o robô estiver ligado, caso contrário, todos os motores são desligados pela função desliga robô.

Figura 23: Liga / Desliga robô

### 3.6.3 Arma

Os motores de arma são comandados pelos botões descritos abaixo.

- BOLINHA - b() == true - liga motores em um sentido
- QUADRADO - x() == true - liga motores em outro sentido
- TRIANGULO - y() == ˆ | true - desliga motores

Recomenda-se desligar os motores antes de inverter o sentido de rotação. Ao inverter o sentido com os motores rotacionando, pode-se danificá-los mecanicamente.


Figura 24: Controle dos motores de arma

A biblioteca segue como referência o controle de Xbox, por isso as funções são b(), x() e y(). Para identificar quais funções se referem aos botões do controle de PS3, basta compará-los.

### 3.6.4 Movimentação

Quando movimentados, os joysticks retornam um valor proporcional ao quão pressionados estão em cada direção (vertical ou horizontal). De acordo com a documentação da Bluepad32, para ambas as direções (horizontal e vertical), o valor retornado pode variar de -511 a 512. O sinal do valor depende do sentido do movimento. Entretanto, os valores podem variar em função do controle utilizado. Para o controle utilizado, tem-se o seguinte comportamento:

- esquerda: retorna um valor horizontal negativo
- direita: retorna um valor horizontal positivo
- cima: retorna um valor vertical negativo
- baixo: retorna um valor vertical positivo

No código do robô, os motores de movimentação podem ser controlados pelo movimento vertical do joystick direito e o movimento horizontal do joystick esquerdo, ou o contrário. Por padrão, é adotada a primeira configuração mencionada, sendo possível alterá-la por meio dos botões R1 e L1, conforme demonstrado na Figura 25 abaixo.


Figura 25: Inversão dos joysticks de movimentação

Os valores vertical e horizontal do joystick esquerdo são retornados pelas funções axisY() e axisX(), respectivamente. Já para o joystick direito, têm-se as funções axisRY() e axisRX() (R = right = direito).


Figura 26: Leitura dos joysticks

Abaixo há uma explicação da lógica de movimentação projetada para o robô em função da movimentação dos joysticks do controle.

- Trás : Direita - Se os joysticks vertical e horizontal forem pressionados para trás (+) e para a direita (+), respectivamente, o robô deve andar para trás e para a direita. Neste caso, o sentido de rotação de ambas as rodas deve ser igual. Entretanto, a velocidade da roda direita deve ser menor que a velocidade da roda esquerda.

Figura 27: Ré para a direita

- Trás : Esquerda - Se os joysticks vertical e horizontal forem pressionados para trás (+) e para a esquerda (-), respectivamente, o robô deve andar para trás e para a esquerda. Neste, o sentido de rotação de ambas as rodas deve ser igual. Entretanto, a velocidade da roda esquerda deve ser menor que a velocidade da roda direita.


Figura 28: Ré para a esquerda

- Ré - Se o joystick vertical for pressionado para trás (+) e o joystick horizontal não for pressionado (0), o robô deve andar para trás apenas. Para esse caso, a velocidade e o sentido de rotação de ambas as rodas devem ser iguais;


Figura 29: Ré

- Frente : Direita - Se os joysticks vertical e horizontal forem pressionados para frente (-) e para a direita (+), respectivamente, o robô deve andar para frente e para a direita. Neste caso, o sentido de rotação de ambas as rodas deve ser igual. Entretanto, a velocidade da roda direita deve ser menor que a da roda esquerda.

Figura 30: Frente para a direita

- Frente : Esquerda - Se os joysticks vertical e horizontal forem pressionados para frente (-) e para a esquerda (-), respectivamente, o robô deve andar para frente e para a esquerda. Para esse caso, o sentido de rotação de ambas as rodas deve ser igual. Entretanto, a velocidade da roda esquerda deve ser menor que a velocidade da roda direita.


Figura 31: Frente para a esquerda

- Frente - Se o joystick vertical for pressionado para frente (-) e o joystick horizontal não for pressionado (0), o robô deve andar apenas para frente. Para esse caso, a velocidade e o sentido de rotação de ambas as rodas devem ser iguais;


Figura 32: Frente

- Rotação horária no próprio eixo - Se o joystick horizontal for pressionado para a direita (+) e o joystick vertical não for pressionado (0), o robô deve rotacionar, no próprio eixo, para o sentido horário. Neste caso, a velocidade de rotação de ambas as rodas deve ser igual, entretanto, a roda da direita deve rodar para trás e a da esquerda, para frente;
- Rotação anti-horária no próprio eixo - Se o joystick horizontal for pressionado para a esquerda (-) e o joystick vertical não for pressionado (nulo), o robô deve rotacionar, no próprio eixo, para o sentido anti-horário. Neste caso, a velocidade de rotação de ambas as rodas deve ser igual, entretanto, a roda da direita deve rodar para frente e a da esquerda, para trás;
- Imobilidade - Se nenhum joystick for pressionado, o robô permanece imóvel.


Figura 33: Rotação no próprio eixo e imobilidade

Para os casos em que uma roda deve rotacionar com velocidade menor do que a outra, de modo que o robô consiga se movimentar simultaneamente para a esquerda ou direita e para frente ou para trás, utiliza-se uma combinação (+ ou -) dos valores vertical e horizontal para encontrar o valor PWM para a roda mais lenta, e apenas o valor vertical para a roda mais rápida. Já para os casos em que ambas as rodas movemse com velocidades iguais, utiliza-se apenas o valor vertical ou o valor horizontal para determinar o valor PWM.

Conforme visto na Apostila de Hardware, a saída analógica da ESP32 é capaz de gerar valores que vão de 0 a 255. Porém, a combinação dos valores dos joysticks pode gerar resultados que vão de -1024 a 1024 nos casos mais extremos. Portanto, é necessário converter o valor da combinação para um valor entre 0 e 255. Para tal, o comando map() foi utilizado.

A função map() recebe como parâmetro o valor que se deseja converter, o limite inferior do intervalo de origem do valor, o limite superior do intervalo de origem do valor, o limite inferior do intervalo de destino do valor e o limite superior do intervalo de destino do valor, nessa ordem. A partir dessas informações, ele calcula um novo valor dentro do intervalo de destino.

= map(valor, deMenor, deM aior, paraMenor, paraM aior); | (1)
1. valor: o número a ser mapeado
2. deMenor: o menor limite do intervalo atual do valor
3. deMaior: o maior limite do intervalo atual do valor
4. paraMenor: o menor limite do intervalo alvo
5. paraMaior: o maior limite do intervalo alvo

Para cada possível combinação dos joysticks (frente + direita, trás + esquerda, ...) existe uma faixa de valores para o intervalo de origem (atual). Entretanto, o intervalo de saída será sempre de 0 a 255 ou de 255 a 0. O código garante que um pino do motor receba um valor baixo de PWM e que o outro receba um valor alto, produzindo assim uma diferença de potência e fazendo com que o motor rotacione. Quanto maior for a diferença entre o PWM de cada pino, maior a rotação do motor.

PARADO JOYSTICK Y e PARADO JOYSTICK X representam os valores que os joysticks retornam na vertical e na horizontal, respectivamente, quando não são movimentados.

MAX JOYSTICK Y e MIN JOYSTICK Y representam, respectivamente, o maior e o menor valor que ambos os joysticks retornam quando verticalmente movimentados (valor quando o joystick é inteiramente pressionado para trás e para frente).

MAX JOYSTICK X e MIN JOYSTICK X representam, respectivamente, o maior e o menor valor que ambos os joysticks retornam quando horizontalmente movimentados (valor quando o joystick é inteiramente pressionado para a direita e para a esquerda).

Esses seis valores variam de controle para controle e podem ser obtidos utilizando um código que será demonstrado mais adiante.

As variáveis MIN PWM e MAX PWM armazenam os limites da faixa PWM para os quais as combinações dos joysticks devem ser convertidas.

Foi definida uma zona morta para o controle, ou seja, se os joysticks forem levemente pressionados, de forma que os valores lidos sejam menores do que a tolerância estipulada, o programa desconsidera o valor lido. Isso foi feito para evitar que o robô fique se movimentando sozinho, devido às vibrações mecânicas no controle e afins.

### 3.6.5 Inversão de rotação dos motores

A lógica de funcionamento da locomoção do robô, descrita no início do subtópico acima, só é válida se os terminais dos motores forem corretamente conectados à placa eletrônica. Para resolver esse problema, projetou-se um trecho de código que permite a troca dos pinos de cada motor. A troca é feita pelas setinhas do controle. Cada setinha representa uma possível combinação de pinos.

Figura 34: Trecho para inversão de rotação dos motores

Por padrão, a configuração da setinha esquerda é assumida sempre que o robô é energizado. Uma vez modificada, o controle permanecerá com a configuração definida. Entretanto, sempre que o robô é desligado, a configuração é perdida, sendo necessário defini-la novamente ao ligá-lo.

### 3.6.6 Trava de configuações

E possível travar a configuração do sentido de rotação dos motores (definido pelas ´ setinhas) e a lógica de funcionamento dos joysticks (definido pelos botões L1 e R1), a fim de evitar alterações caso algum dos botões seja pressionado por engano durante o combate. Para habilitar ou desabilitar tal função, basta apertar simultaneamente os dois joysticks. Um LED azul presente na ESP32 acende quando a trava está habilitada e apaga quando esta está desabilitada.

Figura 35: Trava de configurações

### 3.7 Função setup()

A função setup() é própria da ESP32 e, portanto, é obrigatória para o funcionamento do código. Ela é executada, de forma automática, uma única vez durante todo o funcionamento do programa, no momento em que o controlador é energizado.

De forma geral, neste trecho, colocamos todas as configurações de funcionamento da ESP32 (definição dos pinos de entrada e saída, inicialização da serial, ...), inicializamos as bibliotecas utilizadas e definimos os estados iniciais das variáveis.

No código em questão, primeiramente, inicializa-se a comunicação serial. Ela é utilizada para exibir as mensagens de funcionamento no Monitor Serial, facilitando o entendimento do que está acontecendo. Em sequência, inicializa-se a biblioteca Bluepad32 (observe que as funções de conexão e desconexão do controle são passadas como parâmetro durante a inicialização). Depois definem-se os pinos nos quais as pontes H e o led estão conectados como saída (OUTPUT), utilizando o comando pinMode, e assume-se uma configuração de rotação inicial para os motores de locomoção (equivalente à configuração setinha para a esquerda). Por fim, garante-se que todos os motores e o LED estejam desligados.

### 3.8 Função loop()

Assim que o setup() é executado, a ESP32 passa automaticamente a executar a função loop(). Ela é executada de forma intermitente, ou seja, o controlador executa tudo que está dentro dela; uma vez terminada a execução, volta para o início e executa novamente. Esse processo se repete até que a ESP32 seja desligada. Ela também é própria do controlador e, portanto, é obrigatória para o funcionamento do código.

A função loop() contida no código é bastante reduzida; todo o descritivo do funcionamento do robô está presente na função processControllers(). Neste trecho, há apenas uma verificação de atualização nos dados do controle. Em caso afirmativo, executa-se a função processControllers() para processar os novos dados.


Figura 36: setup()

Figura 37: loop()

## 4 Arquivo parametros.h

Na mesma pasta do código principal, há um arquivo de configurações, denominado parametros.h (.header). Esse arquivo foi criado com o intuito de deixar o código mais organizado, facilitando a alteração de alguns parâmetros caso necessário.

Nas duas primeiras linhas, há a inicialização do arquivo. Se ele não foi definido (if not defined - #ifndef), o definimos (#define) como sendo parametros h. Pode ser que existam arquivos de configuração com o mesmo nome, por isso, esses comandos se fazem necessários. Perceba que o nome na definição deve ser semelhante ao nome do arquivo, diferindo apenas no ponto/underline. O comando #endif encerra o arquivo.

Em sequência, há a inclusão da biblioteca Arduino.h, necessária para que se possa programar na IDE do Arduino e para que alguns comandos sejam compreendidos corretamente.


Figura 38: Inicialização do arquivo .h

Para entender um pouco mais sobre os comandos #ifndef, #endif, entre outros, chamados de diretivas, clique aqui. (https://learn.microsoft.com/pt-br/cpp/preprocessor/preprocessor-directives?view=msvc-170)

Logo abaixo vem a definição dos pinos utilizados para controlar os motores e o led de indicação da trava de configuração (tópico 3.6.6 da apostila). E importante mencionar ´ que a ESP32 vem de fábrica com um LED conectado ao pino D2 da placa, por isso, o led é definido no pino 2. Digitar no código principal o nome escrito após o comando #define é o mesmo que digitar o valor numérico que está do lado direito do nome. Essa definição é importante, pois facilita a identificação dos pinos no código principal.

Figura 39: Defines pinos motores e led

Sobre os dados salvos no arquivo, vêm primeiramente os parâmetros dos joysticks do controle: valores centrais, máximos e mínimos. Em sequência, o valor da zona morta, ou seja, a partir de qual valor deseja-se que o código passe a considerar a leitura do analógico como sendo diferente de 0 (utilizado para evitar trepidações). Por último, há a definição dos limites da faixa de valores que será utilizada para controlar as pontes H. E válido ´ lembrar que estes valores estão relacionados à resolução da saída analógica (PWM) da ESP32.

Para o controle utilizado, os valores retornados por ambos os joysticks, para uma mesma direção e sentido, são idênticos (ex.: quando ambos são pressionados para a esquerda, retornam o mesmo valor). Além disso, ambas as direções possuem a mesma faixa de retorno de valores, conforme demonstrado na Figura 40 abaixo.


Figura 40: Definição de parâmetros

A palavra const no início da definição dos parâmetros indica que eles não mudarão ao longo da execução do código, terão sempre o valor definido no arquivo .h. Sempre que uma dessas variáveis for escrita no código principal, ela estará referenciando o valor descrito nesse arquivo.

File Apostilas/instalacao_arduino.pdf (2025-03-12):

## Instalaçãoda IDE Arduino


Link: https://www.arduino.cc/en/software


Procure o arquivo na pasta onde ele foi salvo. Execute o arquivo para iniciar a instalação.


## Instalaçãoda biblioteca Bluepad32


Link Tutorial Original (https://bluepad32.readthedocs.io/en/latest/plat_arduino/)


https://raw.githubusercontent.com/espressif/arduino-esp32/ghpages/package_esp32_index.json

https://raw.githubusercontent.com/ricardoquesada/esp32-arduino-libbuilder/master/bluepad32_files/package_esp32_bluepad32_index.json

Observação:


As placas ESP32 e Bluepad32 apareceram na foto porque já haviam sido instaladas.


Instale uma placa de cada vez. Caso contrário, a instalação dará erro.


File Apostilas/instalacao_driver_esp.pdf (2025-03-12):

## Instalação do driver CP210x


Link para download: Driver CP210x (https://www.silabs.com/developers/usb-to-uart-bridge-vcp-drivers)


Ao clicar sobre o texto, uma tela abrirá para escolher onde o arquivo será salvo

Extraia o arquivo .zip baixado e abra a pasta que surgir. Você se deparará com os seguintes arquivos:


Com o botão direito, clique sobre o arquivo silabser.inf Depois, clique em Instalar.



Na janela que abrir em sequência, pressione Sim para instalar o drive. Feito isso, ele estará instalado.


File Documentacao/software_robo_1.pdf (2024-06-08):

# Guia

de

# Software

## Índice

### 1. Instalações

### 1.1. Arduino 1.2. Driver

1.

### 3. Bibliotecas

### 2. Linguagem Arduino

### 2.1. Valores

2.

### 1.1. Constantes

### 2.1.1.1. Constantes Booleanas 2.1.1.2. Modos para Pinos Digitais 2.1.1.3. Níveis Lógicos

2.

### 1.2. Tipos de Dados

2.

### 2. Estruturas

2.

### 2.1. Sketch

2.

### 2.2. Elementos de Sintaxe

2.

### 2.3. Estruturas de Controle

2.

### 2.4. Operadores Aritméticos

2.

### 2.5. Operadores de Comparação

2.

### 2.6. Operadores Booleanos

2.

### 3. Funções

2.

### 3.1. Leitura e Escrita de Dados

### 2.3.1.1. Digitais

2.

### 3.1.2. Analógicas

2.

### 3.2. Funções Temporizadoras

2.

### 3.3. Funções Matemáticas

2.

### 3.4. Comunicação

### 3. Código do

robô

### 3.1. Importando bibliotecas 3.2. Definição de variáveis 3.3. Funções

### 3.3.1. desligaRobo() 3.3.2. onConnectedController() 3.3.3. onDisconnectedController() 3.3.4. processControllers()

### 3.4. Movimentação

### 3.4.1. Frente/Direita 3.4.2. Frente/Esquerda 3.4.3. Frente 3.4.4. Ré/Direita 3.4.5. Ré/Esquerda 3.4.6. Ré

### 3.4.7. Direita no eixo 3.4.8. Esquerda no eixo 3.4.9. Imobilidade

### 3.5. setup() 3.6. loop()

### 4. Parametros.h

### 4.1. Determinação de parâmetros

### 5. Filtro MAC

### 1. Instalações

### 1.1. Arduino IDE

A IDE (Integrated Development Environment) Arduino é um software que proporciona um ambiente de desenvolvimento completo para programar microcontroladores como Arduino e ESP32. Ela facilita o processo de escrever códigos e permite que você se concentre mais no desenvolvimento do projeto em si, sem se preocupar com detalhes técnicos complexos. Basicamente, é onde você escreve, edita, compila e carrega seus códigos (sketches) para o seu robô.

Para fazer a instalação, siga as instruções abaixo:

1º passo - Fazer o download do arquivo executável nesse link (https://www.arduino.cc/en/software).


2º passo - Selecionar a opção Just Download.


3º passo - Selecionar novamente a opção Just Download.


4º passo - No Instalador do Arduino IDE concorde com os termos de licença.


5º passo Em seguida escolha a opção de instalação e selecione a opção próximo.

6º passo Em seguida escolha o local da instalação e aperte a opção instalar.


7º passo Completando a instalação aperte em concluir fazendo com que o instalador feche e execute o Arduino IDE.

### 1.2. Driver

Pense que é necessário o seu computador conversar com a ESP para que seja possível enviar os códigos para a ela. Porém, caso você apenas conecte a ESP ao seu computador, ele não será capaz de determinar qual dos dispositivos conectados (mouse, teclado, fone de ouvido, monitor) é o dispositvo em questao. É exatamente nesse momento que entra o driver, para que ele possa especificar para o computador qual dispositivo é o correto para a comunicação de dados. Caso queira saber mais acesse o link: https://learn.microsoft.com/pt-br/windows-hardware/drivers/gettingstarted/what-is-a-driver- (https://learn.microsoft.com/pt-br/windows-hardware/drivers/gettingstarted/what-is-a-driver-)

1º passo - Fazer o download do arquivo executável nesse link (https://www.arduino.cc/en/software) (https://www.silabs.com/developers/usb-to-uart-bridge-vcp-drivers?tab=overview).


2º passo – Selecione a primeira opção de Download.


3º passo – Ao baixar abra a pasta que você realizou o download e selecione o arquivo silabser.


4º passo – Ao abrir o arquivo recebera uma confirmação se deseja abrir precisione abrir normalmente.

5º passo – Apos abrir o driver será instalado assim que a instalação acabar você recebera uma mensagem de confirmação que a instalação esta concluída com êxito basta aperta a opção ok.


### 1.3. Bibliotecas

Pense na biblioteca como sendo um livro de referência que o código vai usar para saber como realizar certas funções. A IDE possui um gerenciador de bibliotecas que facilita a adição das mesmas para expandir as capacidades do microcontrolador, como controlar sensores, módulos Wi-Fi, displays, etc. No nosso caso, vamos usar uma biblioteca para auxiliar no uso do controle por bluetooth.
No menu Sketch, você pode selecionar e incluir no seu projeto as bibliotecas desejadas para realizar funções específicas.
No nosso projeto utilizaremos a biblioteca Bluepad32, a documentação completa da mesma pode ser acessada nesse link (https://bluepad32.readthedocs.io/en/latest/).

1º passo – Abra o Arduino IDE vá em File selecione a opção Preferences (ou utilize o atalho Ctrl + Vírgula).


2º passo – Já na aba Preferences selecione a opção Settings e selecione a opção com dois quadradinho como a imagem abaixo demonstra.

3º passo – Abrindo essa opção você terá o Additional Boards Manager URLs onde você ira colar estes dois links abaixo.
Link 1: https://raw.githubusercontent.com/espressif/arduino-esp32/gh-pages/package_esp32_index.json (https://raw.githubusercontent.com/espressif/arduino-esp32/gh-pages/package_esp32_index.json)
Link 2: https://raw.githubusercontent.com/ricardoquesada/esp32-arduino-lib-builder/master/bluepad32_files/package_esp32_bluepad32_index.json (https://raw.githubusercontent.com/ricardoquesada/esp32-arduino-lib-builder/master/bluepad32_files/package_esp32_bluepad32_index.json)
Em seguida pressione a opção Ok.

4º passo – Voltando para o Arduino IDE vá em Tools selecione a opção Board -> Boards Manager... (ou pressione Ctrl+Shift+B).


5º passo – Em BOARDS MANAGER digite esp32 e realize o install ou o update das bibliotecas esp32 e esp32 bluepad32.


### 2. Linguagem Arduino

A linguagem de programação do Arduino é baseada em C/C++ e será a linguagem que utilizaremos para programar nosso microcontrolador. Ela pode ser dividida em três partes principais: estruturas, valores (variáveis e constantes) e funções.
Abaixo apresentaremos um resumo de cada uma dessas partes, mas caso queira se aprofundar mais no assunto, aconselhamos que consulte a documentação completa do Arduino nesse link (https://www.arduino.cc/reference/pt/).

### 2.1. Valores

Os valores são tipos de dados e constantes da linguagem Arduino, vamos ver alguns deles a seguir.

### 2.1.1. Constantes

Constantes em Arduino são valores que permanecem inalterados durante a execução do programa. Elas são usadas para dar nomes significativos a valores fixos, tornando o código mais legível e fácil de manter. Existem várias maneiras de definir constantes em Arduino, veremos algumas abaixo:

### 2.1.1.1. Constantes Booleanas

Existem duas constantes usadas para representar verdade e falsidade na linguagem Arduino:
- true
Alegação de verdade. Normalmente definido como 1, também pode ter uma definição mais ampla. Qualquer inteiro que não seja zero é considerado true, em um sentido booleano. Então -1, 2 e -200 são todos definidos como true, também, em um sentido booleano.
- false
Alegação de falsidade, é o mais fácil de ser definido. Sendo apenas considerado como false o inteiro 0 (zero).

### 2.1.1.2. Modos para Pinos Digitais

Em Arduino, definir os modos dos pinos digitais é fundamental para controlar como eles interagem com o ambiente externo. A definição de modos é feita com a função pinMode(), que configura um pino específico para operar como entrada (INPUT) ou saída (OUTPUT). Essa configuração será feita dentro do bloco de código setup(), explicado mais à frente. Vamos entender um pouco mais sobre esses modos:
- Entrada (INPUT)
Podemos considerar como entrada todo sinal que será enviado para o microcontrolador partindo do meio externo, como botões ou sensores. Exemplo de configuração de um pino em INPUT:

O trecho de código acima configura o pino 2 do microcontrolador como sendo de entrada.
- Saída (OUTPUT)
Podemos considerar como saída todo sinal que será enviado do microcontrolador para o meio externo, como acionar LEDs ou ligar motores. Exemplo de configuração de um pino em OUTPUT:

O trecho de código acima configura o pino 13 do microcontrolador como sendo de saída.

### 2.1.1.3. Níveis Lógicos

Os níveis lógicos são usados para definir os estados dos pinos digitais, tanto para leitura quanto para escrita. Há apenas dois valores possíveis que esses pinos podem assumir:
- HIGH

Representa nível lógico alto, em estado binário é igual a 1. Isso significa que, no caso de leitura, o retorno seria HIGH se o pino estivesse ligado. Em caso de escrita, você estaria estabelecendo o estado do pino como ligado.
- LOW
Representa nível lógico baixo, em estado binário é igual a 0. Isso significa que, no caso de leitura, o retorno seria LOW se o pino estivesse desligado. Em caso de escrita você estaria estabelecendo o estado do pino como desligado.

### 2.2. Estruturas

As estruturas são os elementos da linguagem Arduino, vamos ver algumas delas a seguir.

### 2.2.1. Sketch

Um esboço é o nome que o Arduino usa para um programa. É a unidade de código que é carregada e executada em uma placa Arduino. Um sketch tem a seguinte estrutura:

Como você pode ver, ele é dividido em dois grandes blocos: setup e loop. Vamos entender um pouquinho mais sobre cada um deles.
A função setup() é chamada quando um sketch inicia. Ela pode ser utilizada para inicializar variáveis, configurar o modo dos pinos (INPUT ou OUTPUT), inicializar bibliotecas, etc. Essa função será executada apenas uma vez, após a placa ser alimentada ou acontecer um reset.
A função loop() faz precisamente o que o seu nome sugere, e repete-se consecutivamente enquanto a placa estiver ligada, permitindo o seu programa mudar e responder a essas mudanças. Use-a para controlar ativamente uma placa Arduino. Sendo assim, podemos dizer que na função setup() colocaremos todas as configurações estáticas do nosso programa e na função loop() colocaremos toda a lógica do nosso programa.

### 2.2.2. Elementos de Sintaxe

Quando programando em linguagem de Arduino, é muito importante se manter atento aos elementos de sintaxe. Eles permitem que seu código fique mais dinâmico e legível. Vamos ver alguns deles abaixo:

- #define
É uma diretiva muito útil que te permite dar um nome a um valor constante antes de o programa ser compilado. Assim, sempre que você for usar aquele valor, poderá chamá-lo pelo seu nome. É importante ressaltar que a declaração de #defines deve ser feita antes, fora dos blocos setup() e loop().

No exemplo acima, definimos que no pino 3 do microcontrolador, se encontra conectado um LED. Portanto, toda vez que formos usar o LED no código, poderemos chamá-lo apenas de LED, sem precisar procurar em qual pino ele está conectado.
- #include
Essa diretiva é usada para incluir bibliotecas (veremos mais sobre esse conceito à frente) externas ao seu sketch. Isso dá acesso a um grande número de bibliotecas padrão da linguagem C (grupos de funções prontas), e também bibliotecas escritas especialmente para a linguagem Arduino.

No exemplo acima, estamos adicionando a biblioteca Bluepad no código, essa será a biblioteca que usaremos para controlar nosso robô.
- Comentários
Comentários são textos no programa normalmente usados para descrever a forma como o programa funciona, eles são ignorados pelo compilador e por isso não atrapalham o funcionamento do código. É uma boa prática fazer sempre comentários que te auxiliem a lembrar o motivo pelo qual o código foi escrito daquela maneira. Os comentários podem ser escritos de duas maneiras:
- Ponto e vírgula
Usado para encerrar um comando. É muito importante ressaltar que o ponto e vírgula não pode ser esquecido! A ausência do ponto e vírgula no final de um comando resulta em erro de compilação. Isso significa que o microcontrolador não vai entender o código e por isso ele não irá executar.
- Chaves
As chaves são usadas em diversas estruturas diferentes, elas delimitam um bloco de códigos que será executado dentro de certas condições. Uma chave "{" deve ser sempre fechada por outra chave "}". Essa é uma condição que é frequentemente chamada de balanceamento das chaves. Assim como o ponto e vírgula, toda chave aberta tem que ser fechada! Caso contrário, seu código pode apresentar erros enigmáticos e muitas vezes difíceis de serem localizados.

### 2.2.3. Estruturas de Controle

Estruturas de controle são comandos que alteram o fluxo de execução do programa, permitindo tomar decisões, repetir blocos de código e controlar o comportamento do programa de maneira dinâmica. Veremos abaixo alguns exemplos:
- if
O comando if checa uma condição e, se a condição é verdadeira, executa o comando a seguir ou um bloco de comandos delimitados por chaves.
- else
A combinação if… else permite maior controle sobre o fluxo de código que o comando mais básico if, por permitir o agrupamento de múltiplos testes. Uma cláusula else será executada se a condição do comando if é falsa.


- else if
O else pode proceder outro teste if, formando então um novo bloco denominado else if. Note que um bloco else if pode ser usado sem um bloco else no final e vice-versa. Um número praticamente ilimitado de blocos else if conectados é permitido.
- for
O comando for é usado para repetir um bloco de código envolvido por chaves. Um contador de incremento é geralmente utilizado para terminar o loop criado pelo for. O comando for é útil para qualquer operação repetitiva, e é usado frequentemente com vetores para operar em coleções de dados ou pinos.

### 2.2.4. Operadores Aritméticos

Os operadores Aritméticos são fundamentais para realizar cálculos matemáticos básicos. Esses operadores são utilizados para manipular variáveis e constantes. Mas é importante ressaltar que a estrutura aqui é diferente da que estamos acostumados! Veremos abaixo alguns exemplos:
- Adição (+)
O operador de adição é usado para somar dois valores.

Então para realizar a soma:
2 + 2 = 4
Na realidade faríamos:

E o resultado seria igual a 4.

- Subtração (-)
O operador de subtração é usado para subtrair dois valores.
- Multiplicação (*)
O operador de multiplicação é usado para multiplicar dois valores.
- Divisão (/)
O operador de divisão é usado para dividir dois valores. É importante ressaltar que, ao dividir inteiros, o resultado será um número inteiro (a parte fracionária é descartada). Para obter resultados de divisão com ponto flutuante, é necessário usar variáveis do tipo float ou double.
- Resto (%)
O operador de resto é usado para obter o restante da divisão de um valor por outro.
- Atribuição (=)
O sinal de igual = na linguagem de programação Arduino é chamado operador de atribuição. Seu significado é diferente das aulas de matemática, onde ele indica uma equação ou igualdade. O operador de atribuição indica ao microcontrolador que compute qualquer valor ou expressão que estiver à direita do sinal de igual, e o armazene na variável à esquerda do sinal de igual.

### 2.2.5. Operadores De Comparação

Os operadores de comparação são fundamentais, eles permitem a avaliação de expressões e são essenciais para estruturas de controle como o if e o for, vistos anteriormente. Veremos abaixo alguns exemplos:
- Igual a (==)
O operador "Igual a" compara a variável à esquerda com o valor ou variável à direita do operador. Retorna verdadeiro (true) quando os dois operandos são iguais.

Exemplo de utilização com a estrutura de controle if:

- Diferente de (!=)
O operador "Diferente de" compara a variável à esquerda com o valor ou variável à direita do operador. Retorna verdadeiro (true) quando os operandos não são iguais.

Exemplo de utilização com a estrutura de controle for:

- Menor que (<)
O operador "Menor que" compara a variável à esquerda com o valor ou variável à direita do operador. Retorna verdadeiro (true) quando o operando à esquerda é menor que o operando à direita.
- Maior que (>)
O operador "Maior que" compara a variável à esquerda com o valor ou variável à direita do operador. Retorna verdadeiro (true) quando o operando à esquerda é maior que o operando à direita.
- Menor que ou igual a (<=)
O operador "Menor que ou igual a" compara a variável à esquerda com o valor ou variável à direita do operador. Retorna verdadeiro (true) quando o operando à esquerda é menor ou igual ao operando à direita.

- Maior que ou igual a (>=)
O operador "Maior que ou igual a" compara a variável à esquerda com o valor ou variável à direita do operador. Retorna verdadeiro (true) quando o operando à esquerda é maior ou igual ao operando à direita.

### 2.2.6. Operadores Booleanos

Os operadores booleanos são essenciais para escrever expressões condicionais e controlar o fluxo do programa. Assim como os operadores de comparação, os operadores booleanos também são essenciais para estruturas de controle como o if e o for. Veremos abaixo alguns exemplos:
- NÃO lógico (!)
O operador "NÃO lógico" resulta em verdadeiro se o operando é falso, e vice-versa. Ele inverte o valor lógico de uma expressão.

No exemplo acima, o valor lógico invertido de y é armazenado em x. Suponhamos que y = true, então o valor armazenado em x seria false.
- E lógico (&&)
O operador "E lógico" resulta em verdadeiro, apenas se ambos operandos são verdadeiros. Caso contrário, ele resulta em falso.
Exemplo utilizando a estrutura de controle if:

No exemplo acima, os comandos seriam executados apenas se ambas condições fossem verdadeiras.
- OU lógico (!)
O operador "OU lógico" resulta em verdadeiro se pelo menos um dos operandos é verdadeiro.
Exemplo utilizando a estrutura de controle for:

No exemplo acima, os comandos seriam executados enquanto pelo menos uma das condições fosse igual.

### 2.3. Funções

Funções são blocos de código que executam tarefas específicas. Existem diversas funções nativas da linguagem, feitas para auxiliar o processo de criação de um código. Vamos ver algumas delas a seguir:

### 2.3.1. Leitura e Escrita de Dados

Já vimos anteriormente o conceito de entrada e saída de dados (INPUT e OUTPUT). Agora precisamos definir como o microcontrolador vai, de fato, utilizar os pinos declarados como sendo de entrada e saída. Para isso, temos algumas funções prontas que realizam a leitura e escrita de dados. Eles podem ser de dois tipos: digitais e analógicos. Vamos entender melhor o funcionamento dessas funções e quando usá-las a seguir.

### 2.3.1.1. Leitura e Escrita Digitais

Um sinal digital é um tipo de sinal que alterna entre dois níveis distintos de tensão, representando os valores binários 0 e 1.
- Modo (pinMode)
Configura o pino especificado para funcionar como uma entrada ou saída. Essa configuração deve ser feita dentro da função setup().
- Leitura (digitalRead)
Lê o valor de um pino digital especificado, e retorna HIGH ou LOW.

No exemplo acima, é realizada a leitura do estado do pino LED. O retorno será HIGH (caso esteja ligado) ou LOW (caso esteja desligado).
- Escrita (digitalWrite)
Aciona um valor HIGH ou LOW em um pino digital.

No exemplo acima, o pino LED recebe o valor HIGH, com isso ele é ligado. Para desligá-lo, bastaria trocar HIGH por LOW.

### 2.3.1.2. Leitura e Escrita Analógicas

Um sinal analógico é um tipo de sinal que varia continuamente ao longo do tempo, podendo assumir qualquer valor dentro de um intervalo específico (no nosso caso, de 0 a 5V).
- Leitura (analogRead)
Lê o valor de um pino digital especificado, e retorna a leitura analógica (int).

No exemplo acima, é realizada a leitura do estado do pino LED. O retorno será um número inteiro que indica o brilho do LED.
- Escrita (analogWrite)
Aciona um valor (int) em um pino analógico.

No exemplo acima, o pino LED recebe o valor 255, isso significa que ele receberá o valor máximo de brilho. Para desligá-lo, bastaria trocar 255 por 0. Valores intermediários também são aceitos para configurar outros níveis de brilho.

### 3. Código do robô

### 3.1. Importando bibliotecas

Nas duas primeiras linhas do programa temos a inclusão da biblioteca utilizada para fazer a comunicação com o controle de PS3 (Bluepad32) (https://bluepad32.readthedocs.io/en/latest/) e a inclusão do arquivo de configurações. O arquivo de configurações será explicado posteriormente.

### 3.2. Definição de variáveis

Logo após as inclusões temos a definição de duas variáveis que serão utilizadas ao longo do programa. A variável myControllers representa o controle que iremos conectar à ESP32. Já a variável roboLigado é um indicador do estado do robô: ligado (verdadeiro/true) ou desligado (falso/false).

### 3.3. Funções

Uma função em Arduino é um bloco de código que executa uma tarefa específica e pode ser chamado repetidamente ao longo do programa. As funções ajudam a organizar e reutilizar o código de forma eficiente.

### 3.3.1. desligaRobo()

A função desligaRobo() contém todos os comandos necessários para interromper o funcionamento do robô. Nas primeiras linhas da função utilizamos o comando digitalWrite para desligar (LOW) as saídas associadas ao controle da arma e ao controle dos motores de movimentação. Em sequência, definimos a velocidade de rotação dos motores de locomoção como sendo 0, utilizando o comando analogWrite. Ao final, definimos o estado do robô como desligado (roboLigado = false).

### 3.3.2. onConnectedController()

A função onConnectedController() é a responsável por conectar o controle à ESP32. Caso deseje realizar alguma tarefa assim que o controle for conectado, basta adicionar o trecho de código no local indicado (entre o comentário e o comando break). É importante ressaltar que a execução dessa função é feita de forma automática pela ESP32, no momento em que há uma conexão/desconexão do controle.

### 3.3.3. onDisconnectedController()

A função onDisconnectedController() é a responsável por desconectar o controle da ESP32. Caso deseje realizar alguma tarefa assim que o controle for desconectado, basta adicionar o trecho de código no local indicado (entre o comentário e o comando break). É importante ressaltar que a execução dessa função é feita de forma automática pela ESP32, no momento em que há uma conexão/desconexão do controle.


Tanto | a | função | onConnectedController() | quanto | a | função
onDisconnectedController()são definidas pela própria biblioteca que estamos utilizando para fazer a interface com o controle (Bluepad32). Entretanto, algumas modificações foram feitas a fim de deixá-las mais simples e compactas.
Uma chamada da função desligaRobo() foi adicionada na função onDisconnectedController() para garantir que o robô pare sua movimentação e sua arma em caso de perda de conexão com o controle (sistema de proteção exigido nas regras de competição da categoria cupim).

### 3.3.4. processControllers()

A função processControllers() é a responsável por mapear o que foi pressionado no controle e, a partir dessas entradas, determinar o funcionamento do robô. Portanto, toda a lógica de funcionamento do robô está descrita dentro desta função.

A primeira tarefa realizada pela função é confirmar se há um dispositivo bluetooth conectado. Logo após, ela também verifica se o dispositivo está enviando dados e se ele é, de fato, um controle (Gamepad). Essa última verificação é feita pois a mesma biblioteca pode ser utilizada para a conexão com diversos tipos de dispositivos bluetooth (mouse, teclado, ...). Se todas essas condições forem satisfeitas, a leitura e o processamento dos dados do controle são feitos.
Feita a verificação da conexão, lê-se o estado dos botões SELECT e START. Se SELECT for pressionado (estadoMiscButtons == 0x02), desliga-se o robô (roboLigado =

false). Caso contrário, se START for pressionado (estadoMiscButtons == 0x04), liga-se o robô (roboLigado = true).

Se o robô estiver ligado, lê-se o estado dos botões (X, O, L1, R1, ...). Se L1 for pressionado (botoesPressionados == 0x0010), desliga-se a arma (LOW). Senão, se R1 for pressionado (botoesPressionados == 0x0020), liga-se a arma (HIGH).

Ainda se o robô estiver ligado, o valor vertical do analógico direito
(valorAnalogicoDireito) | e | o | valor | horizontal | do | analógico | esquerdo
(valorAnalogicoEsquerdo) são lidos e exibidos (Serial.print()) no Monitor Serial.
De forma geral, o analógico retorna um valor negativo se pressionado para a esquerda e um valor positivo se pressionado para a direita. Já na vertical, o analógico retorna um valor negativo se pressionado para cima e um valor positivo se pressionado para baixo. De acordo com a documentação da Bluepad32, para ambas direções, horizontal e vertical, o valor retornado varia de -511 a 512.


O valor vertical do analógico direito está sendo multiplicado por -1 para deixar no mesmo sentido do plano cartesiano (cima +, baixo -), facilitando a compreensão. Considere esta informação ao longo das explicações abaixo.

### 3.4. Movimentação

Feita a leitura dos joysticks, o programa determina a velocidade e o sentido de rotação de cada motor baseado no valor lido. A lógica de determinação é bastante simples:

### 3.4.1. Frente/Direita

Se o analógico direito for pressionado para frente (+) e o analógico esquerdo for pressionado para a direita (+), o robô deve andar para frente e para direita. Para esse caso, a sentido de rotação de ambas rodas deve ser igual. Entretanto, a velocidade da roda esquerda deve ser maior que a velocidade da roda direita, para que o robô vire para a direita.

### 3.4.2. Frente/Esquerda

Se o analógico direito for pressionado para frente (+) e o analógico esquerdo for pressionado para a esquerda (-), o robô deve andar para frente e para esquerda. Para esse caso, a sentido de rotação de ambas as rodas deve ser igual. Entretanto, a velocidade da roda direita deve ser maior que a velocidade da roda esquerda, para que o robô vire para a esquerda.

### 3.4.3. Frente

Se o analógico direito for pressionado para frente (+) e o analógico esquerdo não for pressionado (nulo), o robô deve andar apenas para frente. Para esse caso, a velocidade e o sentido de rotação de ambas as rodas devem ser iguais;

### 3.4.4. Ré/Direita

Se o analógico direito for pressionado para trás (-) e o analógico esquerdo for pressionado para a direita (+), o robô deve andar para trás e para direita. Para esse caso, a sentido de rotação de ambas as rodas deve ser igual. Entretanto, a velocidade da roda esquerda deve ser maior que a velocidade da roda direita, para que o robô vire para a direita.


### 3.4.5. Ré/Esquerda

Se o analógico direito for pressionado para trás (-) e o analógico esquerdo for pressionado para a esquerda (-), o robô deve andar para trás e para esquerda. Para esse caso, a sentido de rotação de ambas as rodas deve ser igual. Entretanto, a velocidade da roda direita deve ser maior que a velocidade da roda esquerda, para que o robô vire para a esquerda.

### 3.4.6. Ré

Se o analógico direito for pressionado para trás (-) e o analógico esquerdo não for pressionado (0), o robô deve andar para trás apenas. Para esse caso, a velocidade e o sentido de rotação de ambas as rodas devem ser iguais;

### 3.4.7. Direita no eixo

Se o analógico esquerdo for pressionado para a direita (+) e o analógico direito não for pressionado (0), o robô deve rotacionar no sentido horário. Para esse caso, a velocidade de rotação de ambas as rodas deve ser igual, entretanto, a roda da direita deve rodar para trás e a da esquerda, para frente (robô rotaciona no próprio eixo);

### 3.4.8. Esquerda no eixo

Se o analógico esquerdo for pressionado para a esquerda (-) e o analógico direito não for pressionado (nulo), o robô deve rotacionar no sentido anti-horário. Para esse caso, a velocidade de rotação de ambas as rodas deve ser igual, entretanto, a roda da direita deve rodar para frente e a da esquerda, para trás (robô rotaciona no próprio eixo);

### 3.4.9. Imobilidade

Se nenhum analógico for pressionado, o robô permanece imóvel.

Foi definida uma zona morta para o controle, ou seja, se os analógicos forem levemente pressionados, de forma que os valores lidos sejam menores do que a tolerância estipulada, o programa desconsidera o valor lido. Isso foi feito para evitar que o robô fique se movimentando sozinho, devido às vibrações mecânicas no controle e afins.
As variáveis centerAnalogR_Y e centerAnalogL_X representam, respectivamente, o valor que o analógico direito e esquerdo retornam quando não estão sendo pressionados.
As variáveis minAnalogR_Y e maxAnalogR_Y representam, respectivamente, o menor e o maior valor que o analógico direito pode retornar quando verticalmente movimentado (valor quando o joystick é inteiramente pressionado trás e para a frente). As variáveis minAnalogL_X e maxAnalogL_X representam, respectivamente, o menor e o maior valor que o analógico esquerdo pode retornar quando horizontalmente movimentado (valor quando o joystick é inteiramente pressionado esquerda e para a direita).
Esses valores variam de controle para controle e podem ser obtidos conectando o controle à ESP32 com a utilização de um programa que será demonstrado mais a diante. Entretanto, é importante lembrar que, no código principal, o valor do analógico direito é multiplicado por -1 ao ser lido. Isso deve ser considerado na hora de definir os limites do controle.
O valor de velocidade colocado em cada roda é proporcional ao valor da combinação entre o valor horizontal do analógico esquerdo e o valor vertical do analógico direito (valorAnalogicoDireito ± valorAnalogicoEsquerdo) e vice-versa. Conforme visto na apostila sobre Hardware, a saída analógica da ESP32 é capaz de gerar valores que vão de 0 a 255. Porém, a combinação dos valores dos analógicos pode gerar resultados que vão de -1024 a 1024 nos casos mais extremos. Portanto, é necessário converter o valor da combinação para um valor entre 0 e 255. Para tal tarefa, utilizamos o comando map(). Ele recebe como parâmetro o valor que se deseja converter, o limite inferior do intervalo de origem do valor, o limite superior do intervalo de origem do valor, o limite inferior do intervalo de destino do valor e o limite superior do intervalo de destino do valor, nessa ordem. A partir dessas informações, ele calcula um novo valor dentro do intervalo de destino.
Para cada possível combinação dos analógicos (frente + direita, trás + esquerda, ...) existe uma faixa de valores para o intervalo de origem. Entretanto, o intervalo de saída será sempre de 0 a 255 ou de 255 a 0.
Para as condições em que os pinos de sentido são configurados como HIGH (analógico direito para frente), deve-se gerar valores de saída de 255 a 0 (0 quando a combinação dos joysticks atingir o valor máximo). Já para as condições em que os pinos de sentido são configurados como LOW (analógico direito para trás), deve-se gerar valores de saída de 0 a 255 (255 quando a combinação dos joysticks atingir o valor máximo). Isso se deve ao de funcionamento da ponte H. Caso queira se aprofundar mais na lógica de funcionamento da ponte H, consulte o manual (datasheet).

Finalizada a etapa de determinação, escreve-se os valores de velocidade nas saídas analógicas.


Caso o robô seja/esteja desligado, os trechos de código contendo o mapeamento dos botões e dos analógicos e todo o processo de cálculo das velocidades será ignorado, a arma será desligada e a velocidade dos motores definida para 0.

### 3.5. setup()

A função setup() é própria da ESP32 e, portanto, é obrigatória para o funcionamento do código. Ela é executada, de forma automática, uma única vez durante todo o funcionamento do programa: no momento em que o controlador é energizado.

De forma geral, neste trecho colocamos todas as configurações de funcionamento da ESP32 (definição dos pinos de entrada e saída, inicialização da serial, ...), inicializamos as bibliotecas utilizadas e definimos os estados iniciais das variáveis.

No código que estamos utilizando, primeiramente inicializamos a comunicação serial. É esta comunicação que utilizamos para exibir as mensagens de funcionamento no monitor serial. Em sequência, inicializamos a biblioteca Bluepad32 e removemos todos os dispositivos que haviam sido pareados anteriormente. Perceba que as funções de conexão e desconexão do controle são passadas como parâmetro durante a inicialização. Depois definimos os pinos nos quais a ponte H e o motor da arma estão conectados como saída (OUTPUT), utilizando o comando pinMode, e as desligamos (desligaRobo()).

### 3.6. loop()

Assim que o setup() é executado, a ESP32 passa automaticamente a executar a função loop(). Ela é executada de forma interrupta, ou seja, o controlador executa tudo que está dentro dela, uma vez terminada a execução, volta para o início e executa novamente. Esse processo se repete até que a ESP32 seja desligada. Ela também é própria do controlador e, portanto, é obrigatória para o funcionamento do código.
A função loop() contida em nosso código é bastante reduzida, pois fizemos todo o descritivo do funcionamento do robô na função processControllers(). Neste trecho apenas verificamos se houve atualização nos dados do controle e, em caso afirmativo, executamos a função processControllers().

### 4. Parametros.h

Na mesma pasta do código principal há um arquivo de configurações, denominado parametros.h (.header). Esse arquivo foi criado com o intuito de deixar o código mais organizado, facilitando a alteração de alguns parâmetros caso necessário. Nas duas primeiras linhas temos o início do arquivo. Se ele não tiver sido definido (if not defined - #ifndef), o definimos(#define) como sendo parametros_h. Pode ser que tenhamos arquivos de configuração com o mesmo nome, por isso esses comandos se fazem necessários. Perceba que o nome na definição deve ser semelhante ao nome do arquivo, diferindo apenas no ponto/underline.

Obs: Caso queira conhecer um pouco mais sobre essas diretivas, consulte esse link. (https://learn.microsoft.com/pt-br/cpp/preprocessor/preprocessor-directives?view=msvc-170) (https://learn.microsoft.com/pt-br/cpp/preprocessor/preprocessor-directives?view=msvc-170)
Em sequência, incluímos a biblioteca Arduino.h, necessária para que possamos programar na IDE do Arduino e para que alguns comandos sejam compreendidos corretamente.

Logo abaixo vem a definição dos pinos que estamos utilizando para controlar a arma e os motores de movimentação. Ao digitarmos no código o nome escrito após o comando #define estamos na verdade digitando o valor numérico que está do lado direito do nome. Essa definição é importante pois facilita a identificação dos pinos no código principal.

Temos agora a definição de alguns parâmetros. Primeiramente vem os parâmetros dos analógicos do controle: valores centrais, máximos e mínimos. Em sequência, o valor da zona morta, ou seja, a partir de qual valor desejamos que o código passe a considerar a leitura do analógico como sendo diferente de 0, utilizado para evitar trepidações. Por último temos a definição dos limites da faixa de valores que será utilizada para controlar a ponte H. É valido lembrar que estes valores estão relacionados à resolução da saída analógica (PWM) da ESP32.
A palavra const no início da definição dos parâmetros indica que eles não mudarão ao longo da execução do código, terão sempre o valor definido no arquivo .h. Sempre que uma dessas variáveis for escrita no código principal ela estará referenciando o valor descrito nesse arquivo.

Na última linha do programa temos o comando #endif, encerrando a diretiva #ifndef que está no início do arquivo.

### 4.1. Determinação de parâmetros

Conforme visto anteriormente, para o correto cálculo dos valores de velocidade de cada roda do robô é necessário determinar a faixa de valores retornada por cada analógico do controle (vide explicação da função processControllers() no tópico sobre o
código | principal). | Para | tal | tarefa | iremos | utilizar | o | programa
descobrir_parametos_controle, disponível no repositório que você baixou no GitHub (https://github.com/nrc-cupim/cupim).

Ao abrir esse código, você irá perceber que ele é bastante semelhante ao código principal visto anteriormente, o diferencial está apenas nasfunções processControllers() e onConnectedController().
Na função onConnectedController() foram adicionadas 4 novas linhas de código, que tem como principal objetivo fazer a leitura do endereço MAC do controle (em um tópico posterior irei explicar a funcionalidade desse endereço). Por enquanto, apenas anote o endereço que será exibido quando executarmos esse programa.

Já a função processControllers() teve sua lógica substituída por um mapeamento de todas as entradas do controle. Ao executar o código e pressionar/mover os botões do controle, é possível ver como a ESP32 interpreta cada parâmetro.



Façamos agora um teste. Com o controle conectado, pressione a tecla SELECT e veja o que acontece com o valor da variável misc. Repita o processo para a tecla START. Por meio desses testes é possível entender as comparações (estadoMiscButtons == 0x02) e (estadoMiscButtons == 0x04) feitas no código principal.


O mesmo raciocino se aplica à lógica de acionamento/desligamento da arma. A partir do código de determinação dos parâmetros é possível alterar o funcionamento do robô (código principal) para a forma que achar melhor (configurar o acionamento e o desligamento do robô para os botões O e X, por exemplo). Para tal, basta fazer a leitura do parâmetro e comprar com o valor desejado. Por exemplo:

Esse mesmo código deve ser utilizado para fazer a determinação dos parâmetros centerAnalogR, centerAnalogL, minAnalogR, minAnalogL, maxAnalogR e maxAnalogL utilizados ao longo do código principal para definição do sentido e velocidade de rotação das rodas. Uma vez medidos, basta registra-los no arquivo parâmetros.h.

Obs: Não esqueça que os valores do analógico direito devem ser multiplicados por -1 antes de serem colocados no arquivo (vide explicação do código principal)
É importante mencionar que controles diferentes podem ter comportamentos diferentes. Portanto, é recomendado testar cada controle antes de utiliza-lo para pilotar o robô.

### 5. Filtro MAC

Conforme mencionado anteriormente, cada controle possui um identificador, denominado endereço MAC. Este endereço é único para cada controle e serve para identificar dispositivos em uma conexão, permitindo que as mensagens sejam encaminhadas corretamente entre origem e destino.

Quando conectamos a ESP32 ao controle estamos na verdade estabelecendo uma conexão bluetooth entre esses dispositivos, permitindo que eles troquem dados entre si.

Pensando em um cenário de competição, é fácil perceber que poderão existir vários controles próximos ao robô. Portanto, é recomendado informar à ESP32 em qual controle ela deve se conectar, evitando que o sinal de outro controle interfira na comunicação e, por consequência, no funcionamento do robô.

Para implementar tal filtro, basta utilizar o código filtro_mac_controle, disponível na pasta que você baixo do GitHub (https://github.com/nrc-cupim/cupim).

Esse código habilita uma lista de permissões na ESP32 e adiciona endereços a ela. Dessa forma, apenas dispositivos adicionados à lista poderão se conectar ao controlador.

O endereço adicionado será armazenado na memória não volátil das ESP (NVS – Non volatile storage), assim como a configuração da lista de permissões. Isso significa que se o dispositivo reiniciar ou se outro código for carregado para ele, tanto o endereço quanto a configuração da lista de permissões ainda estarão salvos.

Para utilizar o código, o primeiro passo é escrever o endereço MAC do controle, obtido com o código descobrir_parametros_controle (também disponível no repositório do GitHub), no local informado.


Dentro da função setup(), o primeiro passo é converter o endereço MAC que acabamos de definir para uma forma de endereço compreensível pela ESP32. Para tal tarefa, utiliza-se a função sscanf_bd_addr(). Ela recebe como parâmetro o endereço MAC que se deseja converter e a variável onde o endereço convertido será salvo. Feita a conversão, o próximo passo é adicionar o endereço à lista de permissão utilizando a função uni_bt_allowlist_add_addr(). Ela recebe como parâmetro o endereço MAC convertido que se deseja adicionar á lista. Caso deseje remover um

endereço | adicionado | anteriormente, | basta | utilizar | o | comando
uni_bt_allowlist_remove_addr().

É possível armazenar até quatro endereços MAC na memória da ESP, permitindo a conexão de 4 controles distintos. Supondo que quatro endereços já estejam armazenados na memória é necessário remover um antes de adicionar outro. É importante comentar também que caso endereços duplicados sejam adicionados, nada acontece.

Por fim, a função uni_bt_allowlist_set_enabled() é a responsável por ativar/desativar a lista de permissões. Caso true seja passado como argumento para a ela, habilita-se a lista de permissões. Já false desabilita.


Ao carregar o código para a ESP32, o filtro passa a valer. O próximo passo é carregar o código principal para o controlador e validar o funcionamento do filtro.


Link | do | tutorial | utilizado | como | base:
https://bluepad32.readthedocs.io/en/latest/FAQ/#how-to-pair-just-one-controller-to-one-particular-board (https://bluepad32.readthedocs.io/en/latest/FAQ/)

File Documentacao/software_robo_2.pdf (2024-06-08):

# Guia

de

# Software

## Índice

### 1. Instalações

### 1.1. Arduino 1.2. Driver

1.

### 3. Bibliotecas

### 2. Linguagem Arduino

### 2.1. Valores

2.

### 1.1. Constantes

### 2.1.1.1. Constantes Booleanas 2.1.1.2. Modos para Pinos Digitais 2.1.1.3. Níveis Lógicos

2.

### 1.2. Tipos de Dados

2.

### 2. Estruturas

2.

### 2.1. Sketch

2.

### 2.2. Elementos de Sintaxe

2.

### 2.3. Estruturas de Controle

2.

### 2.4. Operadores Aritméticos

2.

### 2.5. Operadores de Comparação

2.

### 2.6. Operadores Booleanos

2.

### 3. Funções

2.

### 3.1. Leitura e Escrita de Dados

### 2.3.1.1. Digitais

2.

### 3.1.2. Analógicas

2.

### 3.2. Funções Temporizadoras

2.

### 3.3. Funções Matemáticas

2.

### 3.4. Comunicação

### 3. Código do

robô

### 3.1. Importando bibliotecas 3.2. Definição de variáveis 3.3. Funções

### 3.3.1. desligaRobo() 3.3.2. onConnectedController() 3.3.3. onDisconnectedController() 3.3.4. processControllers()

### 3.4. Movimentação

### 3.4.1. Frente/Direita 3.4.2. Frente/Esquerda 3.4.3. Frente 3.4.4. Ré/Direita 3.4.5. Ré/Esquerda 3.4.6. Ré

### 3.4.7. Direita no eixo 3.4.8. Esquerda no eixo 3.4.9. Imobilidade

### 3.5. setup() 3.6. loop()

### 4. Parametros.h

### 4.1. Determinação de parâmetros

### 5. Filtro MAC

### 1. Instalações

### 1.1. Arduino IDE

A IDE (Integrated Development Environment) Arduino é um software que proporciona um ambiente de desenvolvimento completo para programar microcontroladores como Arduino e ESP32. Ela facilita o processo de escrever códigos e permite que você se concentre mais no desenvolvimento do projeto em si, sem se preocupar com detalhes técnicos complexos. Basicamente, é onde você escreve, edita, compila e carrega seus códigos (sketches) para o seu robô.

Para fazer a instalação, siga as instruções abaixo:

1º passo - Fazer o download do arquivo executável nesse link (https://www.arduino.cc/en/software).


2º passo - Selecionar a opção Just Download.


3º passo - Selecionar novamente a opção Just Download.


4º passo - No Instalador do Arduino IDE concorde com os termos de licença.


5º passo Em seguida escolha a opção de instalação e selecione a opção próximo.

6º passo Em seguida escolha o local da instalação e aperte a opção instalar.


7º passo Completando a instalação aperte em concluir fazendo com que o instalador feche e execute o Arduino IDE.

### 1.2. Driver

Pense que é necessário o seu computador conversar com a ESP para que seja possível enviar os códigos para a ela. Porém, caso você apenas conecte a ESP ao seu computador, ele não será capaz de determinar qual dos dispositivos conectados (mouse, teclado, fone de ouvido, monitor) é o dispositvo em questao. É exatamente nesse momento que entra o driver, para que ele possa especificar para o computador qual dispositivo é o correto para a comunicação de dados. Caso queira saber mais acesse o link: https://learn.microsoft.com/pt-br/windows-hardware/drivers/gettingstarted/what-is-a-driver- (https://learn.microsoft.com/pt-br/windows-hardware/drivers/gettingstarted/what-is-a-driver-)

1º passo - Fazer o download do arquivo executável nesse link (https://www.arduino.cc/en/software) (https://www.silabs.com/developers/usb-to-uart-bridge-vcp-drivers?tab=overview).


2º passo – Selecione a primeira opção de Download.


3º passo – Ao baixar abra a pasta que você realizou o download e selecione o arquivo silabser.


4º passo – Ao abrir o arquivo recebera uma confirmação se deseja abrir precisione abrir normalmente.

5º passo – Apos abrir o driver será instalado assim que a instalação acabar você recebera uma mensagem de confirmação que a instalação esta concluída com êxito basta aperta a opção ok.


### 1.3. Bibliotecas

Pense na biblioteca como sendo um livro de referência que o código vai usar para saber como realizar certas funções. A IDE possui um gerenciador de bibliotecas que facilita a adição das mesmas para expandir as capacidades do microcontrolador, como controlar sensores, módulos Wi-Fi, displays, etc. No nosso caso, vamos usar uma biblioteca para auxiliar no uso do controle por bluetooth.
No menu Sketch, você pode selecionar e incluir no seu projeto as bibliotecas desejadas para realizar funções específicas.
No nosso projeto utilizaremos a biblioteca Bluepad32, a documentação completa da mesma pode ser acessada nesse link (https://bluepad32.readthedocs.io/en/latest/).

1º passo – Abra o Arduino IDE vá em File selecione a opção Preferences (ou utilize o atalho Ctrl + Vírgula).


2º passo – Já na aba Preferences selecione a opção Settings e selecione a opção com dois quadradinho como a imagem abaixo demonstra.

3º passo – Abrindo essa opção você terá o Additional Boards Manager URLs onde você ira colar estes dois links abaixo.
Link 1: https://raw.githubusercontent.com/espressif/arduino-esp32/gh-pages/package_esp32_index.json (https://raw.githubusercontent.com/espressif/arduino-esp32/gh-pages/package_esp32_index.json)
Link 2: https://raw.githubusercontent.com/ricardoquesada/esp32-arduino-lib-builder/master/bluepad32_files/package_esp32_bluepad32_index.json (https://raw.githubusercontent.com/ricardoquesada/esp32-arduino-lib-builder/master/bluepad32_files/package_esp32_bluepad32_index.json)
Em seguida pressione a opção Ok.

4º passo – Voltando para o Arduino IDE vá em Tools selecione a opção Board -> Boards Manager... (ou pressione Ctrl+Shift+B).


5º passo – Em BOARDS MANAGER digite esp32 e realize o install ou o update das bibliotecas esp32 e esp32 bluepad32.


### 2. Linguagem Arduino

A linguagem de programação do Arduino é baseada em C/C++ e será a linguagem que utilizaremos para programar nosso microcontrolador. Ela pode ser dividida em três partes principais: estruturas, valores (variáveis e constantes) e funções.
Abaixo apresentaremos um resumo de cada uma dessas partes, mas caso queira se aprofundar mais no assunto, aconselhamos que consulte a documentação completa do Arduino nesse link (https://www.arduino.cc/reference/pt/).

### 2.1. Valores

Os valores são tipos de dados e constantes da linguagem Arduino, vamos ver alguns deles a seguir.

### 2.1.1. Constantes

Constantes em Arduino são valores que permanecem inalterados durante a execução do programa. Elas são usadas para dar nomes significativos a valores fixos, tornando o código mais legível e fácil de manter. Existem várias maneiras de definir constantes em Arduino, veremos algumas abaixo:

### 2.1.1.1. Constantes Booleanas

Existem duas constantes usadas para representar verdade e falsidade na linguagem Arduino:
- true
Alegação de verdade. Normalmente definido como 1, também pode ter uma definição mais ampla. Qualquer inteiro que não seja zero é considerado true, em um sentido booleano. Então -1, 2 e -200 são todos definidos como true, também, em um sentido booleano.
- false
Alegação de falsidade, é o mais fácil de ser definido. Sendo apenas considerado como false o inteiro 0 (zero).

### 2.1.1.2. Modos para Pinos Digitais

Em Arduino, definir os modos dos pinos digitais é fundamental para controlar como eles interagem com o ambiente externo. A definição de modos é feita com a função pinMode(), que configura um pino específico para operar como entrada (INPUT) ou saída (OUTPUT). Essa configuração será feita dentro do bloco de código setup(), explicado mais à frente. Vamos entender um pouco mais sobre esses modos:
- Entrada (INPUT)
Podemos considerar como entrada todo sinal que será enviado para o microcontrolador partindo do meio externo, como botões ou sensores. Exemplo de configuração de um pino em INPUT:

O trecho de código acima configura o pino 2 do microcontrolador como sendo de entrada.
- Saída (OUTPUT)
Podemos considerar como saída todo sinal que será enviado do microcontrolador para o meio externo, como acionar LEDs ou ligar motores. Exemplo de configuração de um pino em OUTPUT:

O trecho de código acima configura o pino 13 do microcontrolador como sendo de saída.

### 2.1.1.3. Níveis Lógicos

Os níveis lógicos são usados para definir os estados dos pinos digitais, tanto para leitura quanto para escrita. Há apenas dois valores possíveis que esses pinos podem assumir:
- HIGH

Representa nível lógico alto, em estado binário é igual a 1. Isso significa que, no caso de leitura, o retorno seria HIGH se o pino estivesse ligado. Em caso de escrita, você estaria estabelecendo o estado do pino como ligado.
- LOW
Representa nível lógico baixo, em estado binário é igual a 0. Isso significa que, no caso de leitura, o retorno seria LOW se o pino estivesse desligado. Em caso de escrita você estaria estabelecendo o estado do pino como desligado.

### 2.2. Estruturas

As estruturas são os elementos da linguagem Arduino, vamos ver algumas delas a seguir.

### 2.2.1. Sketch

Um esboço é o nome que o Arduino usa para um programa. É a unidade de código que é carregada e executada em uma placa Arduino. Um sketch tem a seguinte estrutura:

Como você pode ver, ele é dividido em dois grandes blocos: setup e loop. Vamos entender um pouquinho mais sobre cada um deles.
A função setup() é chamada quando um sketch inicia. Ela pode ser utilizada para inicializar variáveis, configurar o modo dos pinos (INPUT ou OUTPUT), inicializar bibliotecas, etc. Essa função será executada apenas uma vez, após a placa ser alimentada ou acontecer um reset.
A função loop() faz precisamente o que o seu nome sugere, e repete-se consecutivamente enquanto a placa estiver ligada, permitindo o seu programa mudar e responder a essas mudanças. Use-a para controlar ativamente uma placa Arduino. Sendo assim, podemos dizer que na função setup() colocaremos todas as configurações estáticas do nosso programa e na função loop() colocaremos toda a lógica do nosso programa.

### 2.2.2. Elementos de Sintaxe

Quando programando em linguagem de Arduino, é muito importante se manter atento aos elementos de sintaxe. Eles permitem que seu código fique mais dinâmico e legível. Vamos ver alguns deles abaixo:

- #define
É uma diretiva muito útil que te permite dar um nome a um valor constante antes de o programa ser compilado. Assim, sempre que você for usar aquele valor, poderá chamá-lo pelo seu nome. É importante ressaltar que a declaração de #defines deve ser feita antes, fora dos blocos setup() e loop().

No exemplo acima, definimos que no pino 3 do microcontrolador, se encontra conectado um LED. Portanto, toda vez que formos usar o LED no código, poderemos chamá-lo apenas de LED, sem precisar procurar em qual pino ele está conectado.
- #include
Essa diretiva é usada para incluir bibliotecas (veremos mais sobre esse conceito à frente) externas ao seu sketch. Isso dá acesso a um grande número de bibliotecas padrão da linguagem C (grupos de funções prontas), e também bibliotecas escritas especialmente para a linguagem Arduino.

No exemplo acima, estamos adicionando a biblioteca Bluepad no código, essa será a biblioteca que usaremos para controlar nosso robô.
- Comentários
Comentários são textos no programa normalmente usados para descrever a forma como o programa funciona, eles são ignorados pelo compilador e por isso não atrapalham o funcionamento do código. É uma boa prática fazer sempre comentários que te auxiliem a lembrar o motivo pelo qual o código foi escrito daquela maneira. Os comentários podem ser escritos de duas maneiras:
- Ponto e vírgula
Usado para encerrar um comando. É muito importante ressaltar que o ponto e vírgula não pode ser esquecido! A ausência do ponto e vírgula no final de um comando resulta em erro de compilação. Isso significa que o microcontrolador não vai entender o código e por isso ele não irá executar.
- Chaves
As chaves são usadas em diversas estruturas diferentes, elas delimitam um bloco de códigos que será executado dentro de certas condições. Uma chave "{" deve ser sempre fechada por outra chave "}". Essa é uma condição que é frequentemente chamada de balanceamento das chaves. Assim como o ponto e vírgula, toda chave aberta tem que ser fechada! Caso contrário, seu código pode apresentar erros enigmáticos e muitas vezes difíceis de serem localizados.

### 2.2.3. Estruturas de Controle

Estruturas de controle são comandos que alteram o fluxo de execução do programa, permitindo tomar decisões, repetir blocos de código e controlar o comportamento do programa de maneira dinâmica. Veremos abaixo alguns exemplos:
- if
O comando if checa uma condição e, se a condição é verdadeira, executa o comando a seguir ou um bloco de comandos delimitados por chaves.
- else
A combinação if… else permite maior controle sobre o fluxo de código que o comando mais básico if, por permitir o agrupamento de múltiplos testes. Uma cláusula else será executada se a condição do comando if é falsa.


- else if
O else pode proceder outro teste if, formando então um novo bloco denominado else if. Note que um bloco else if pode ser usado sem um bloco else no final e vice-versa. Um número praticamente ilimitado de blocos else if conectados é permitido.
- for
O comando for é usado para repetir um bloco de código envolvido por chaves. Um contador de incremento é geralmente utilizado para terminar o loop criado pelo for. O comando for é útil para qualquer operação repetitiva, e é usado frequentemente com vetores para operar em coleções de dados ou pinos.

### 2.2.4. Operadores Aritméticos

Os operadores Aritméticos são fundamentais para realizar cálculos matemáticos básicos. Esses operadores são utilizados para manipular variáveis e constantes. Mas é importante ressaltar que a estrutura aqui é diferente da que estamos acostumados! Veremos abaixo alguns exemplos:
- Adição (+)
O operador de adição é usado para somar dois valores.

Então para realizar a soma:
2 + 2 = 4
Na realidade faríamos:

E o resultado seria igual a 4.

- Subtração (-)
O operador de subtração é usado para subtrair dois valores.
- Multiplicação (*)
O operador de multiplicação é usado para multiplicar dois valores.
- Divisão (/)
O operador de divisão é usado para dividir dois valores. É importante ressaltar que, ao dividir inteiros, o resultado será um número inteiro (a parte fracionária é descartada). Para obter resultados de divisão com ponto flutuante, é necessário usar variáveis do tipo float ou double.
- Resto (%)
O operador de resto é usado para obter o restante da divisão de um valor por outro.
- Atribuição (=)
O sinal de igual = na linguagem de programação Arduino é chamado operador de atribuição. Seu significado é diferente das aulas de matemática, onde ele indica uma equação ou igualdade. O operador de atribuição indica ao microcontrolador que compute qualquer valor ou expressão que estiver à direita do sinal de igual, e o armazene na variável à esquerda do sinal de igual.

### 2.2.5. Operadores De Comparação

Os operadores de comparação são fundamentais, eles permitem a avaliação de expressões e são essenciais para estruturas de controle como o if e o for, vistos anteriormente. Veremos abaixo alguns exemplos:
- Igual a (==)
O operador "Igual a" compara a variável à esquerda com o valor ou variável à direita do operador. Retorna verdadeiro (true) quando os dois operandos são iguais.

Exemplo de utilização com a estrutura de controle if:

- Diferente de (!=)
O operador "Diferente de" compara a variável à esquerda com o valor ou variável à direita do operador. Retorna verdadeiro (true) quando os operandos não são iguais.

Exemplo de utilização com a estrutura de controle for:

- Menor que (<)
O operador "Menor que" compara a variável à esquerda com o valor ou variável à direita do operador. Retorna verdadeiro (true) quando o operando à esquerda é menor que o operando à direita.
- Maior que (>)
O operador "Maior que" compara a variável à esquerda com o valor ou variável à direita do operador. Retorna verdadeiro (true) quando o operando à esquerda é maior que o operando à direita.
- Menor que ou igual a (<=)
O operador "Menor que ou igual a" compara a variável à esquerda com o valor ou variável à direita do operador. Retorna verdadeiro (true) quando o operando à esquerda é menor ou igual ao operando à direita.

- Maior que ou igual a (>=)
O operador "Maior que ou igual a" compara a variável à esquerda com o valor ou variável à direita do operador. Retorna verdadeiro (true) quando o operando à esquerda é maior ou igual ao operando à direita.
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

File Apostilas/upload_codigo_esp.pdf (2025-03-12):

## Configurandocontrole


Execute o arquivo .ino dentro da pasta filtro_mac_controle


Link do tutorial original: FAQ Bluepad32 (https://bluepad32.readthedocs.io/en/latest/FAQ/)




Obs.: o computador pode mostrar um número diferente de 1 na frente do escrito COM


Feito isso, o filtro de conexão via MAC já estará funcionando. O próximo passo é carregar o código principal

## Carregando código principal


Escolha a pasta em função do modelo do seu robô e do modelo do controle. Execute o arquivo .ino que estiver dentro de uma das pastas e carregue o código.


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

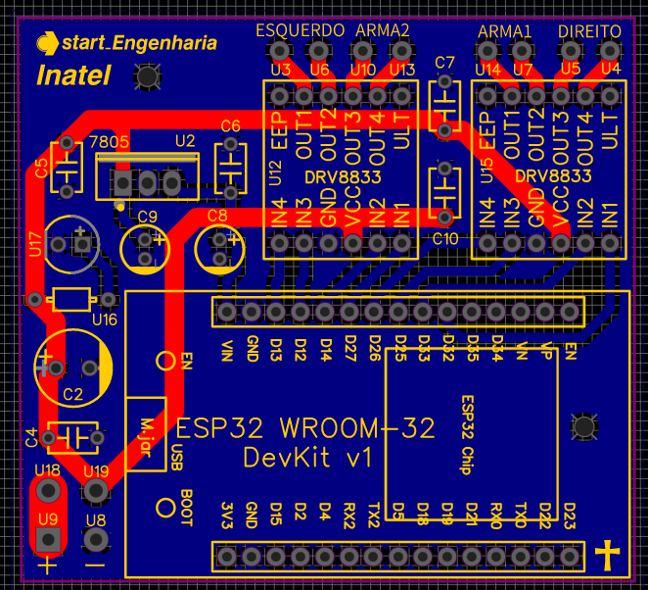
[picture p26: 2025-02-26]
Hardware/board_placa.png

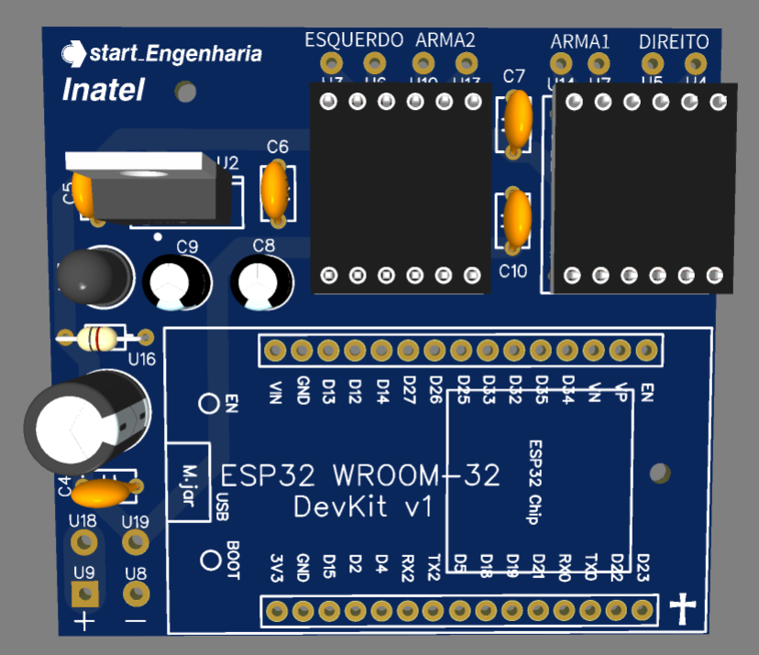
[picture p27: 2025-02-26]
Hardware/vista_superior_3D_placa.png

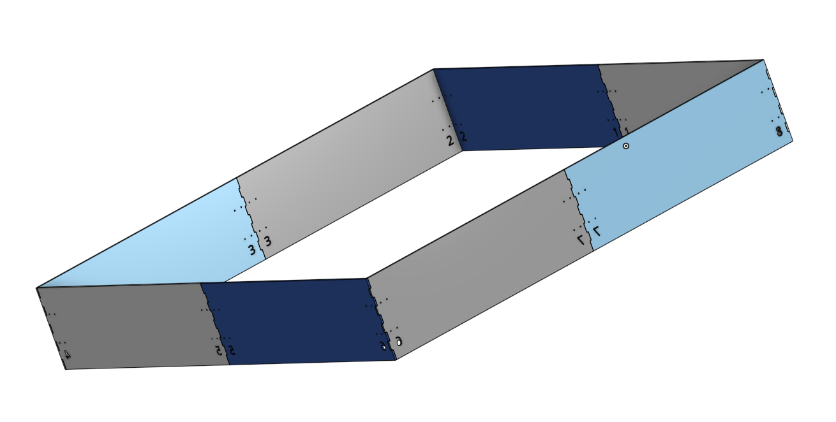
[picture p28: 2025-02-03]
Mecanica/Arena_MDF/foto_estrutura.PNG

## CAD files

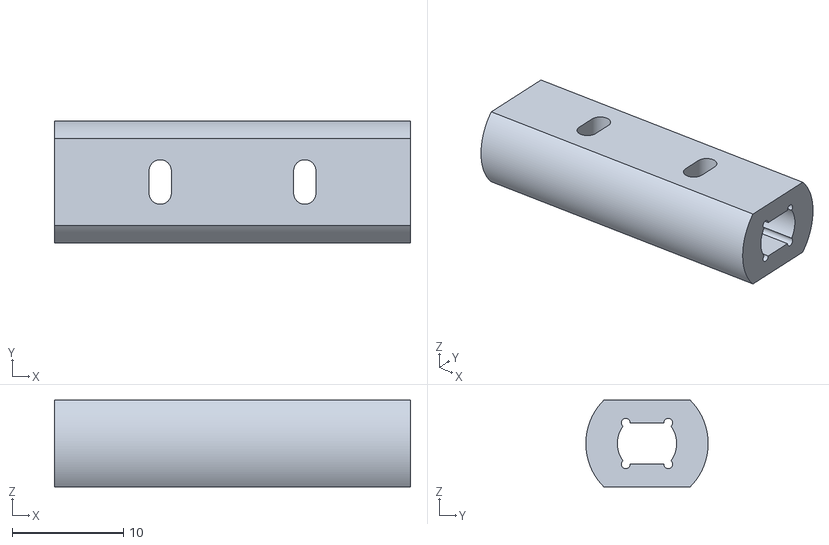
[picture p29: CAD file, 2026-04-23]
Mecanica/2026_robos/armas/eixo_arma_3d.stl
32.0 x 11.0 x 7.78

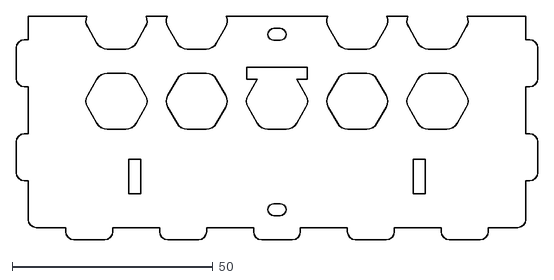
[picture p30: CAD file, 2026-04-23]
Mecanica/2026_robos/carcaca/topo_traseira.dxf
130.0 x 55.7

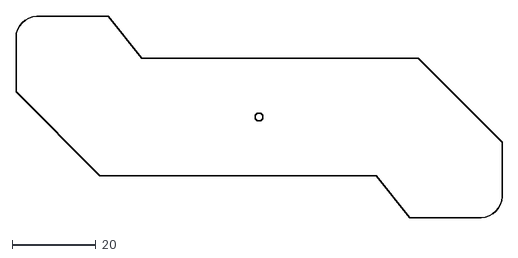
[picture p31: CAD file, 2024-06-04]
Mecanica/robo_1/Arma2.dxf
116.0 x 48.0

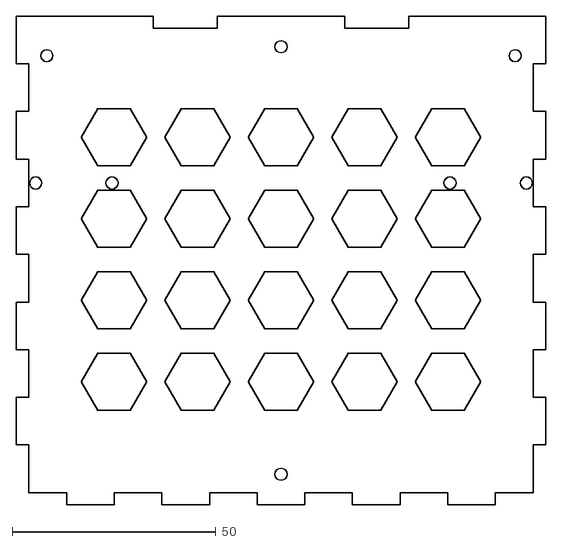
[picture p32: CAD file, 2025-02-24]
Mecanica/Robo_1/DXFs/Base.dxf
130.0 x 120.0

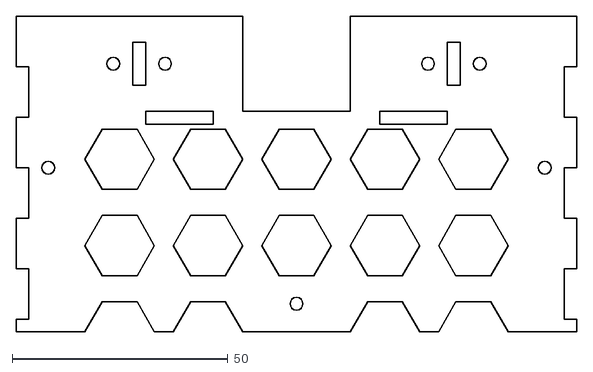
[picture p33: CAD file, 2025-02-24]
Mecanica/Robo_2/DXFs/topo1.dxf
130.0 x 73.2

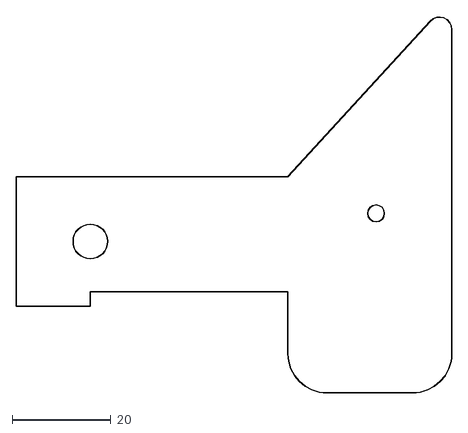
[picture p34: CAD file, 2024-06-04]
Mecanica/robo_2/Suporte Encaixe Prego.dxf
88.2 x 76.3

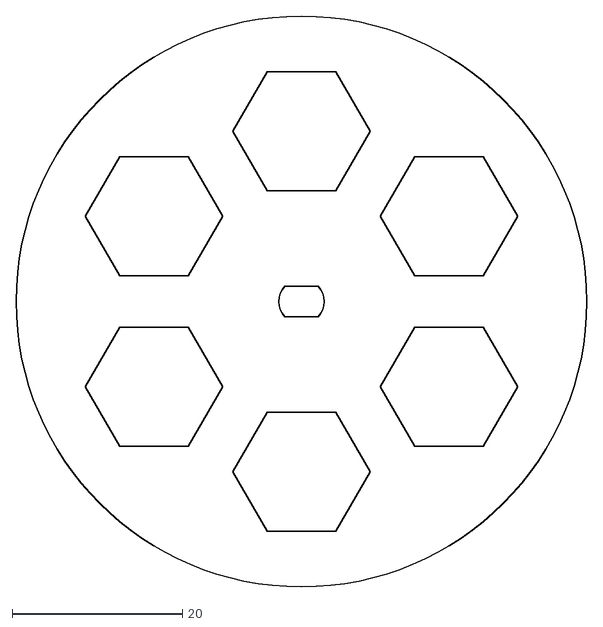
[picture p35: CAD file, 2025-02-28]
Mecanica/roda_mdf/roda.dxf
67.0 x 67.0

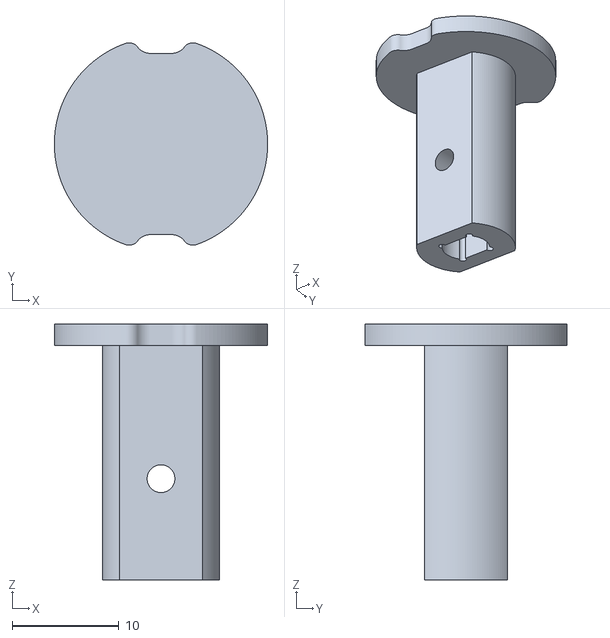
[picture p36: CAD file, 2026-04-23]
Mecanica/rodas_mdf_eixo_3d/eixo_hub_3d_1.stl
20.0 x 19.0 x 24.0

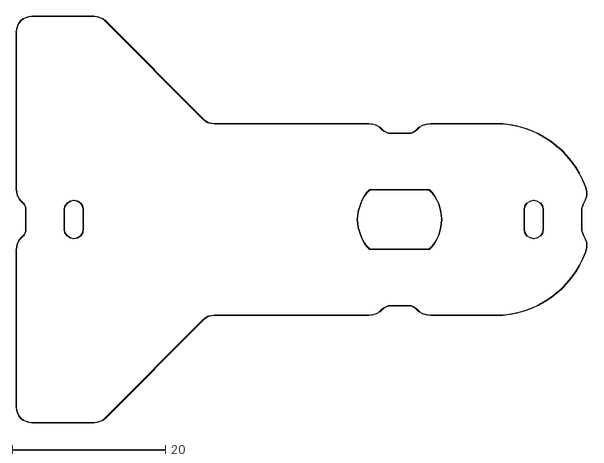
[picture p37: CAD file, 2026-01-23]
Mecanica/2026_robos/armas/arma_meio_martelo.dxf
74.5 x 53.0

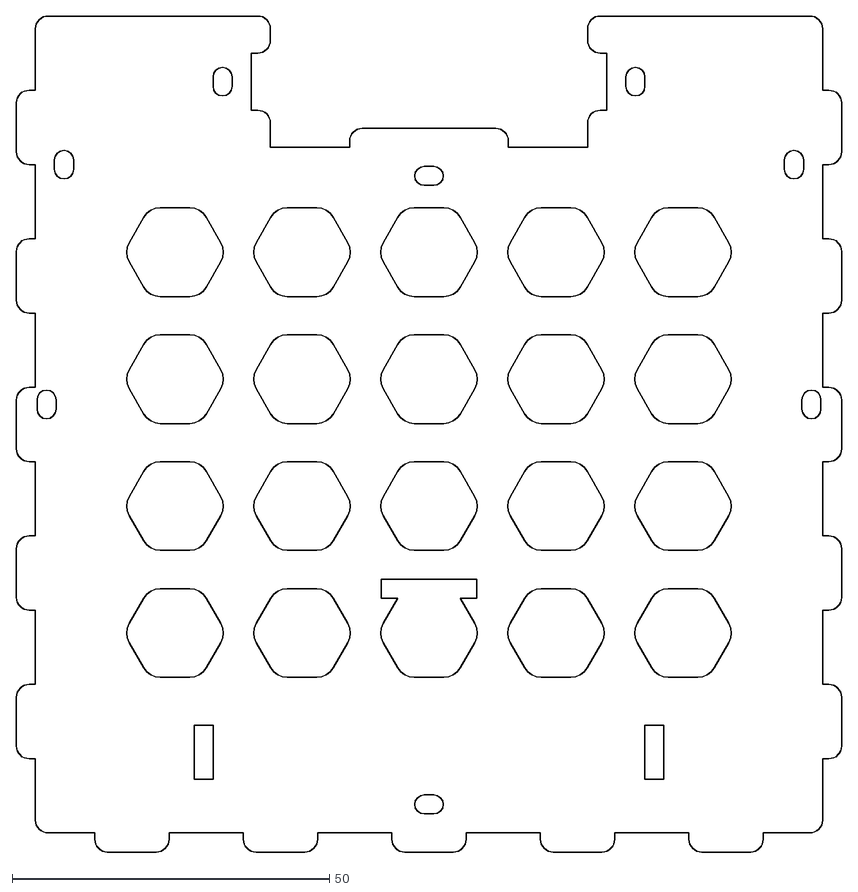
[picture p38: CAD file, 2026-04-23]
Mecanica/2026_robos/carcaca/base.dxf
130.0 x 131.7

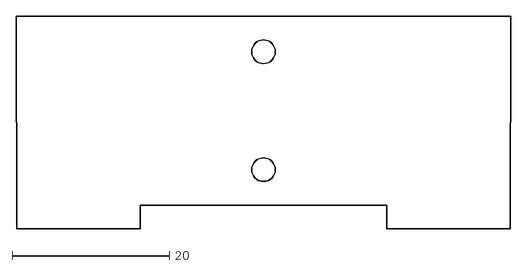
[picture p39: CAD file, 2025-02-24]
Mecanica/Robo_1/DXFs/frente.dxf
62.9 x 27.0

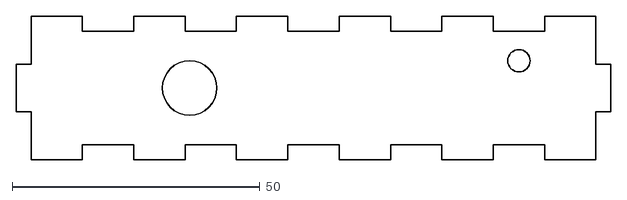
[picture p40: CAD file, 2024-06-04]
Mecanica/robo_1/Lateral - Part 2.dxf
120.0 x 29.0

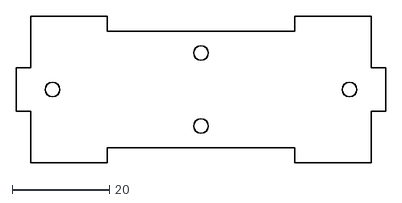
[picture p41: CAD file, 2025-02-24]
Mecanica/Robo_2/DXFs/frente.dxf
75.9 x 30.0

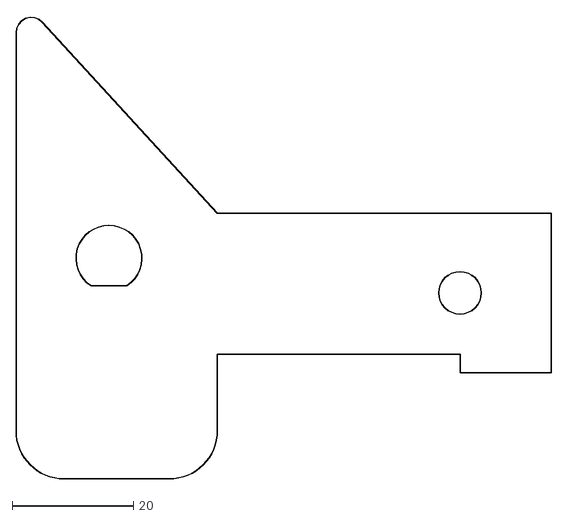
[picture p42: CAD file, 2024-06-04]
Mecanica/robo_2/Suporte Motor - Part 2.dxf
88.2 x 76.3

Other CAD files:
Mecanica/roda_mdf/extensor.dxf
Mecanica/rodas_mdf_eixo_3d/eixo_hub_3d_2.stl
Mecanica/2026_robos/armas/arma_martelo.dxf
Mecanica/2026_robos/carcaca/lateral2.dxf
Mecanica/2026_robos/armas/arma_curva.dxf
Mecanica/2026_robos/armas/arma_meia_curva.dxf
Mecanica/2026_robos/carcaca/apoio_torre.dxf
Mecanica/2026_robos/carcaca/frente.dxf
Mecanica/2026_robos/carcaca/lateral1.dxf
Mecanica/2026_robos/carcaca/torre_motor.dxf
Mecanica/Robo_1/DXFs/Arma.dxf
Mecanica/Robo_1/DXFs/Traseira.dxf
Mecanica/Robo_1/DXFs/lateral1.dxf
Mecanica/Robo_1/DXFs/lateral2.dxf
Mecanica/Robo_1/DXFs/topo1.dxf
Mecanica/Robo_1/DXFs/topo2.dxf
Mecanica/Robo_2/DXFs/Arma sem furo.dxf
Mecanica/Robo_2/DXFs/Arma.dxf
Mecanica/Robo_2/DXFs/Base.dxf
Mecanica/Robo_2/DXFs/Traseira.dxf
Mecanica/Robo_2/DXFs/lateral1.dxf
Mecanica/Robo_2/DXFs/lateral2.dxf
Mecanica/Robo_2/DXFs/topo2.dxf
Mecanica/Robo_2/DXFs/torre.dxf
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

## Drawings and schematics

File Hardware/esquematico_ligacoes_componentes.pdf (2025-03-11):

## CHAVE

## Alimentacao, seccionamento, filtragem e sinalizacao

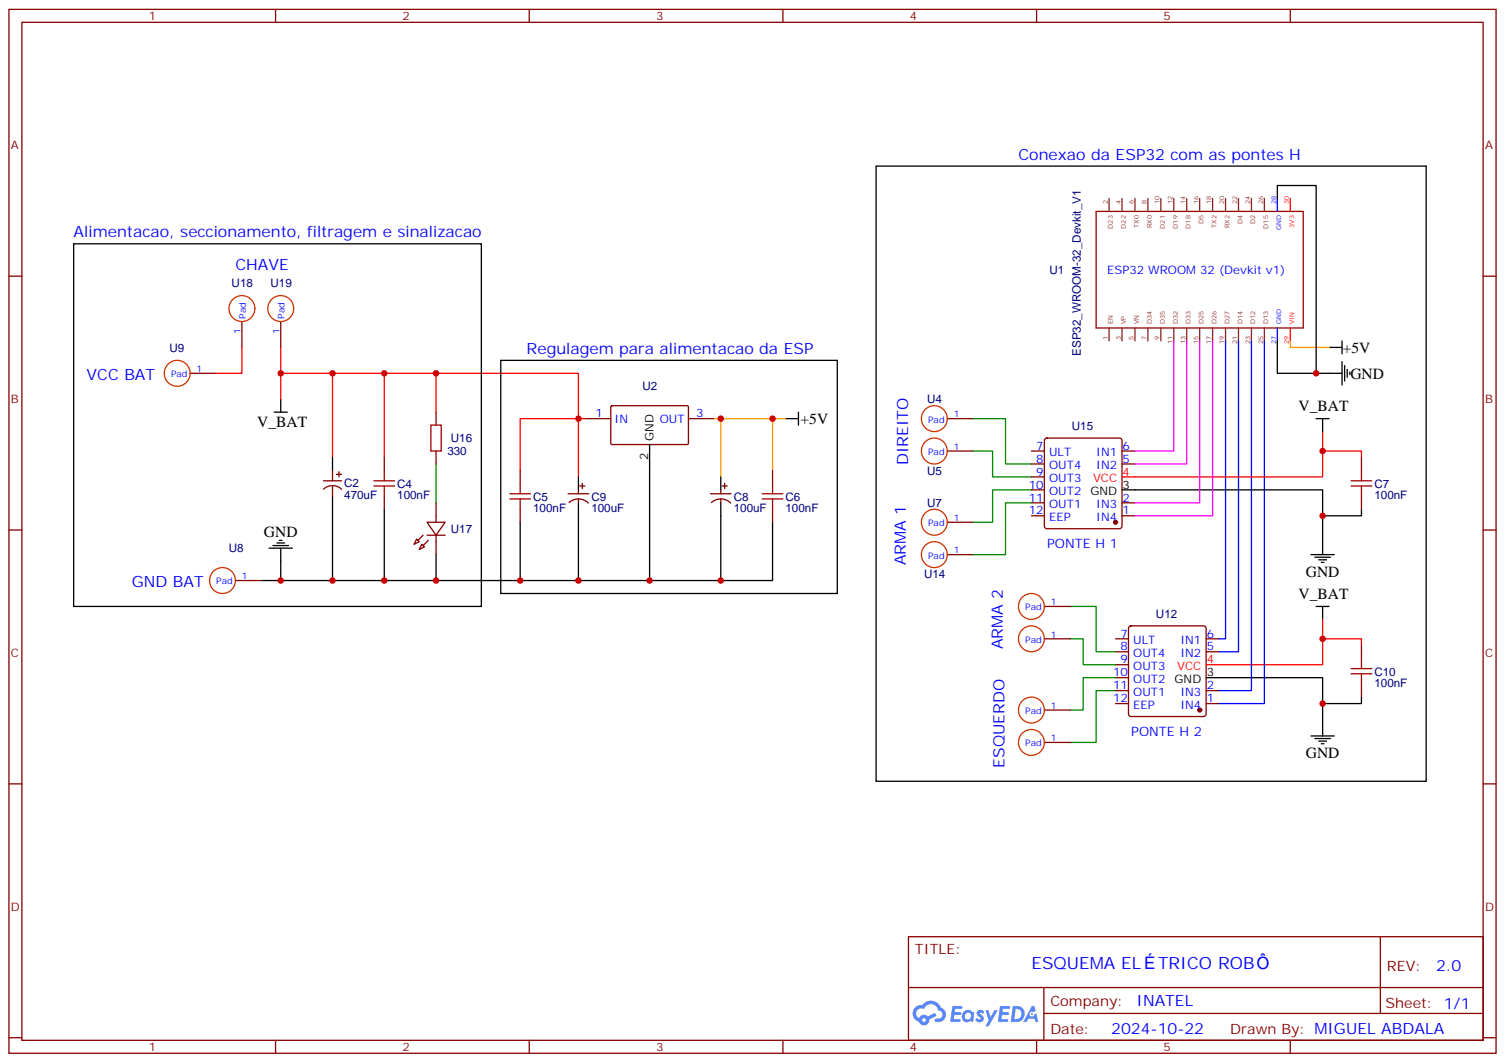
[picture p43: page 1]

Conexao da ESP32 com as pontes H

Regulagem para alimentacao da ESP

Drawn By: MIGUEL ABDALA

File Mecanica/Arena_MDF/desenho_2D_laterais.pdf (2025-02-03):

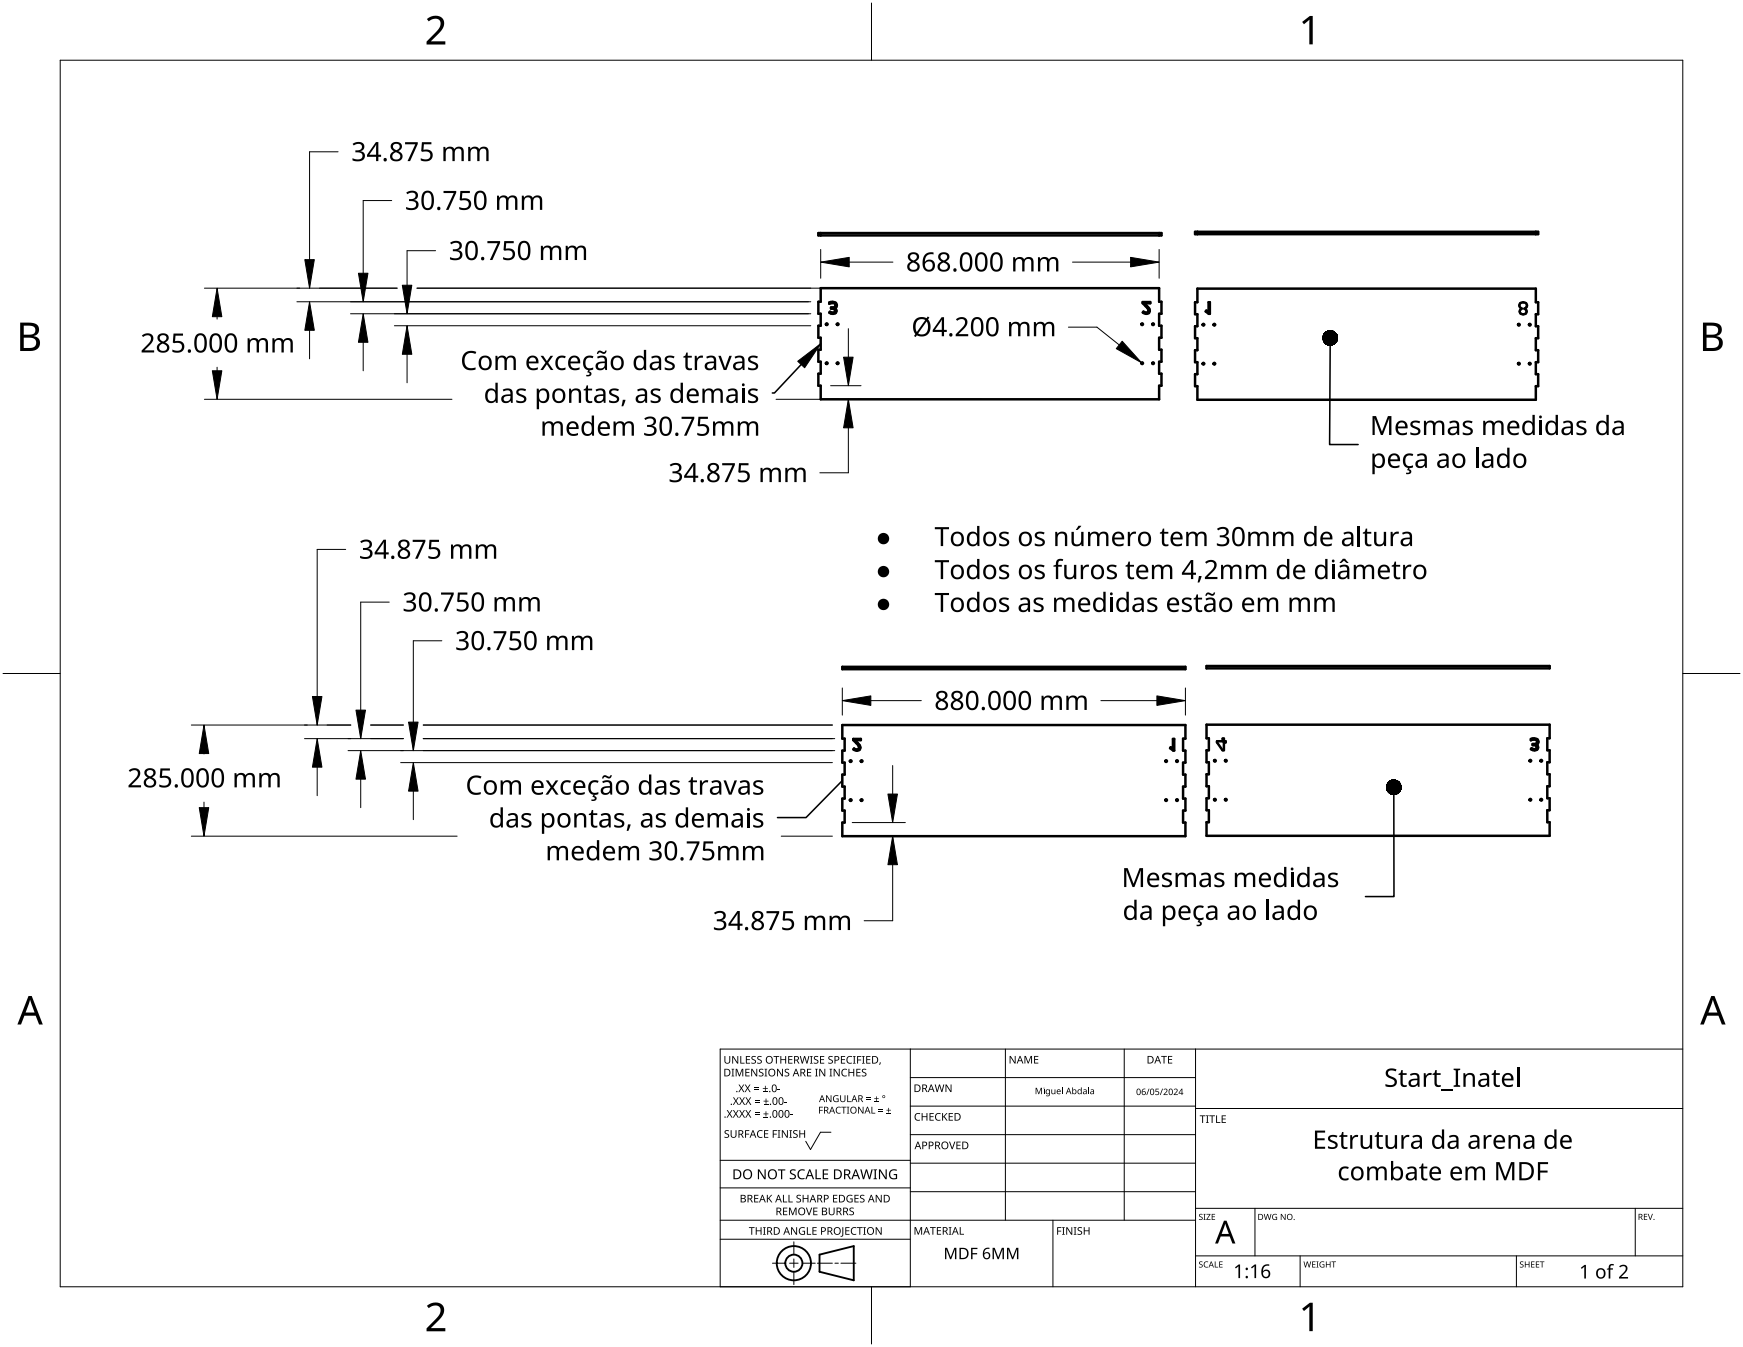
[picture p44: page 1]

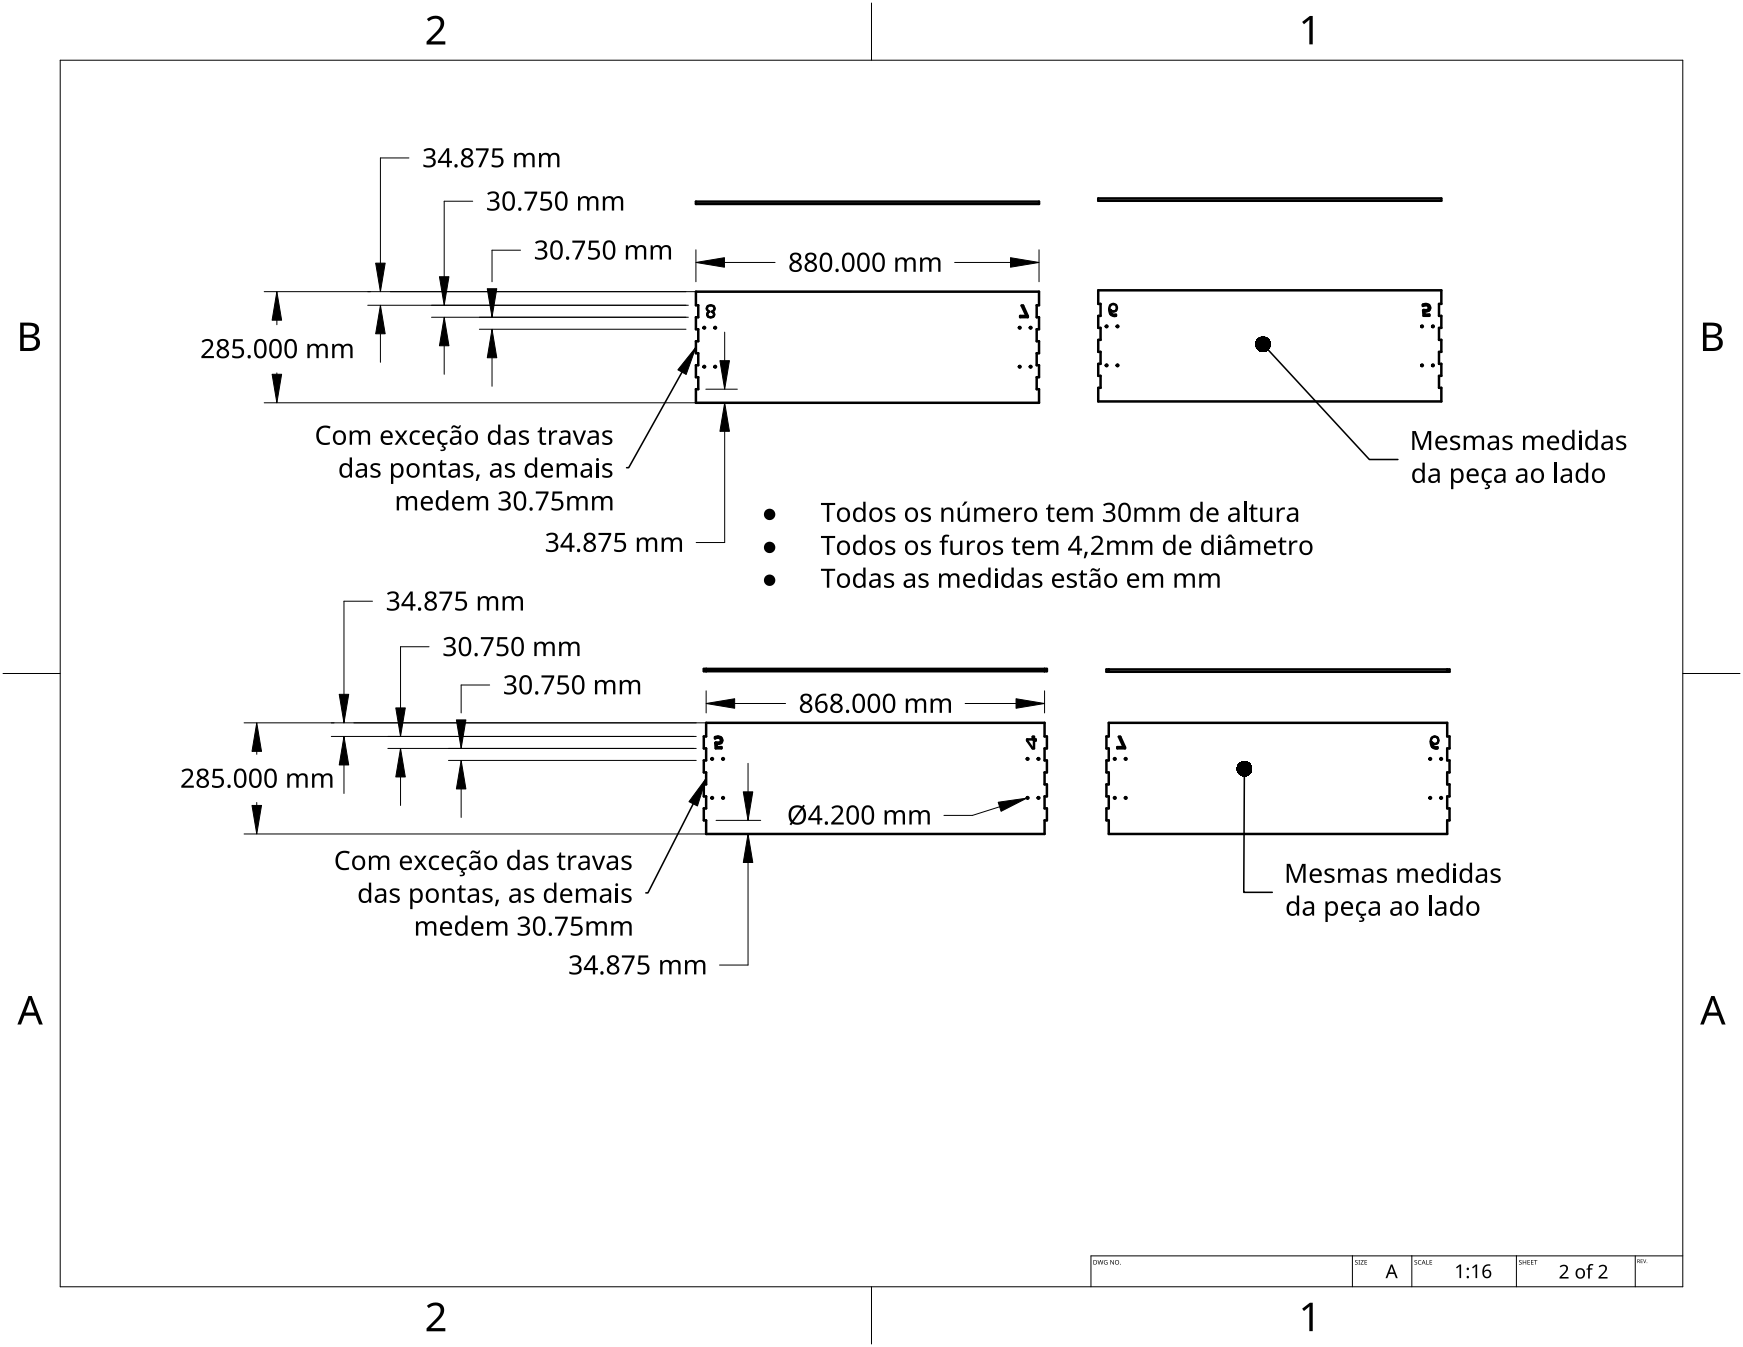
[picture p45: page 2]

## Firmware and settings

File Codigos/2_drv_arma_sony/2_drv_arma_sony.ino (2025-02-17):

#include <Bluepad32.h>
#include "parametros.h"

ControllerPtr myControllers[BP32_MAX_GAMEPADS];
bool roboLigado;

void desligaRobo() {
  analogWrite(PINO1_ARMA1, 0);
  analogWrite(PINO2_ARMA1, 0);

  analogWrite(PINO1_ARMA2, 0);
  analogWrite(PINO2_ARMA2, 0);

  digitalWrite(SENTIDO_MOTOR_ESQUERDO, LOW);
  analogWrite(VELOCIDADE_MOTOR_ESQUERDO, 0);

  digitalWrite(SENTIDO_MOTOR_DIREITO, LOW);
  analogWrite(VELOCIDADE_MOTOR_DIREITO, 0);

  roboLigado = false;
}

void onConnectedController(ControllerPtr ctl) {

  bool foundEmptySlot = false;

  for (int i = 0; i < BP32_MAX_GAMEPADS; i++) {
    if (myControllers[i] == nullptr) {
      Serial.println("AVISO: controle conectado.");
      myControllers[i] = ctl;
      foundEmptySlot = true;

      /* Caso deseje realizar alguma tarefa assim que a conexão 
         com o contole for estabelecidada, coloque o código aqui. */

      break;
    }
  }

  if (!foundEmptySlot) {
    Serial.println("AVISO: Nao foi possivel conectar o controle.");
    Serial.println("AVISO: Reinicie a ESP32 e tente novamente.");
  }
}

void onDisconnectedController(ControllerPtr ctl) {
  for (int i = 0; i < BP32_MAX_GAMEPADS; i++) {
    if (myControllers[i] == ctl) {
      Serial.printf("AVISO: controle desconectado");
      myControllers[i] = nullptr;
      desligaRobo();

      /* Caso deseje realizar alguma tarefa assim que o 
         controle for desconectado, coloque o código aqui */

      break;
    }
  }
}

void processControllers() {
  for (auto myController : myControllers) {

    if (myController && myController->isConnected()
        && myController->hasData() && myController->isGamepad()) {

      /* A partir daqui inicia-se a lógica de funcionamento do robô.
         Qualquer alteração / nova implementação deve ser feita aqui. */

      uint16_t estadoMiscButtons = myController->miscButtons();

      // Se SELECT for presionado, desliga robô.
      if (estadoMiscButtons == 0x02) {
        roboLigado = false;
        Serial.println("Robo desligado");
      }

      // Se START for presionado, liga robô.
      else if (estadoMiscButtons == 0x04) {
        roboLigado = true;
        Serial.println("Robo iniciado");
      }

      if (roboLigado) {

        uint16_t botoesPressionados = myController->buttons();

        // Se TRIÂNGULO for presionado, desliga motores da arma.
        if (botoesPressionados == 0x0008) {
          Serial.print("Arma desligada\n");

          analogWrite(PINO1_ARMA1, 0);
          analogWrite(PINO2_ARMA1, 0);

          analogWrite(PINO1_ARMA2, 0);
          analogWrite(PINO2_ARMA2, 0);
        }

        //Se BOLINHA for pressionado, roda arma para um lado
        if (botoesPressionados == 0x0002) {
          Serial.print("Arma Sentido 1\n");

          analogWrite(PINO1_ARMA1, 0);
          analogWrite(PINO2_ARMA1, maxPWM);

          analogWrite(PINO1_ARMA2, maxPWM);  // para rodar pro outro lado
          analogWrite(PINO2_ARMA2, 0);
        }

        // Se QUADRADO for pressionado, roda arma para o outro lado
        else if (botoesPressionados == 0x0004) {
          Serial.print("Arma Sentido 2\n");

          analogWrite(PINO1_ARMA1, maxPWM);
          analogWrite(PINO2_ARMA1, 0);

          analogWrite(PINO1_ARMA2, 0);  // para rodar pro outro lado
          analogWrite(PINO2_ARMA2, maxPWM);
        }

        // Lê valor em Y do analógico direito (R-right).
        int32_t valorAnalogicoDireito = -myController->axisRY();

        // Lê valor em X do analógico esquerdo (L-left).
        int32_t valorAnalogicoEsquerdo = myController->axisX();

        // Exibe valores no monitor serial.

        Serial.print("Y analogico R: ");
        Serial.println(valorAnalogicoDireito);

        Serial.print("X analogico L: ");
        Serial.println(valorAnalogicoEsquerdo);

        int pwmMotorDireito, pwmMotorEsquerdo;

        if (valorAnalogicoDireito > (centerAnalogR_Y + toleranciaAnalogico)) {

          digitalWrite(SENTIDO_MOTOR_DIREITO, HIGH);
          digitalWrite(SENTIDO_MOTOR_ESQUERDO, HIGH);

          if (valorAnalogicoEsquerdo > (centerAnalogL_X + toleranciaAnalogico)) {

            pwmMotorDireito = map(valorAnalogicoDireito - valorAnalogicoEsquerdo,
                                  centerAnalogR_Y - maxAnalogL_X,
                                  maxAnalogR_Y - centerAnalogL_X,
                                  maxPWM,
                                  minPWM);

            pwmMotorEsquerdo = map(valorAnalogicoDireito + valorAnalogicoEsquerdo,
                                   centerAnalogR_Y + centerAnalogL_X,
                                   maxAnalogR_Y + maxAnalogL_X,
                                   maxPWM,
                                   minPWM);
          }

          else if (valorAnalogicoEsquerdo < (centerAnalogL_X - toleranciaAnalogico)) {

            pwmMotorDireito = map(valorAnalogicoDireito - valorAnalogicoEsquerdo,
                                  centerAnalogR_Y - centerAnalogL_X,
                                  maxAnalogR_Y - minAnalogL_X,
                                  maxPWM,
                                  minPWM);

            pwmMotorEsquerdo = map(valorAnalogicoDireito + valorAnalogicoEsquerdo,
                                   centerAnalogR_Y + minAnalogL_X,
                                   maxAnalogR_Y + centerAnalogL_X,
                                   maxPWM,
                                   minPWM);
          }

          else {
            pwmMotorDireito = map(valorAnalogicoDireito, centerAnalogR_Y, maxAnalogR_Y, maxPWM, minPWM);
            pwmMotorEsquerdo = map(valorAnalogicoDireito, centerAnalogR_Y, maxAnalogR_Y, maxPWM, minPWM);
          }
        }

        else if (valorAnalogicoDireito < (centerAnalogR_Y - toleranciaAnalogico)) {

          digitalWrite(SENTIDO_MOTOR_DIREITO, LOW);
          digitalWrite(SENTIDO_MOTOR_ESQUERDO, LOW);

          if (valorAnalogicoEsquerdo > (centerAnalogL_X + toleranciaAnalogico)) {
            pwmMotorDireito = map(valorAnalogicoEsquerdo + valorAnalogicoDireito,
                                  centerAnalogL_X + minAnalogL_X,
                                  maxAnalogL_X + centerAnalogR_Y,
                                  minPWM,
                                  maxPWM);

            pwmMotorEsquerdo = map(valorAnalogicoEsquerdo - valorAnalogicoDireito,
                                   centerAnalogL_X - centerAnalogR_Y,
                                   maxAnalogL_X - minAnalogR_Y,
                                   minPWM,
                                   maxPWM);
          }

          else if (valorAnalogicoEsquerdo < (centerAnalogL_X - toleranciaAnalogico)) {
            pwmMotorDireito = map(valorAnalogicoEsquerdo + valorAnalogicoDireito,
                                  centerAnalogL_X + centerAnalogR_Y,
                                  minAnalogL_X + minAnalogR_Y,
                                  minPWM,
                                  maxPWM);

            pwmMotorEsquerdo = map(valorAnalogicoEsquerdo - valorAnalogicoDireito,
                                   minAnalogL_X - centerAnalogR_Y,
                                   centerAnalogL_X - minAnalogR_Y,
                                   minPWM,
                                   maxPWM);
          }

          else {
            pwmMotorDireito = map(valorAnalogicoDireito, centerAnalogR_Y, minAnalogR_Y, minPWM, maxPWM);
            pwmMotorEsquerdo = map(valorAnalogicoDireito, centerAnalogR_Y, minAnalogR_Y, minPWM, maxPWM);
          }
        }

        else {

          if (valorAnalogicoEsquerdo > (centerAnalogL_X + toleranciaAnalogico)) {
            digitalWrite(SENTIDO_MOTOR_DIREITO, LOW);
            digitalWrite(SENTIDO_MOTOR_ESQUERDO, HIGH);
            pwmMotorDireito = map(valorAnalogicoEsquerdo, centerAnalogL_X, maxAnalogL_X, minPWM, maxPWM);
            pwmMotorEsquerdo = map(valorAnalogicoEsquerdo, centerAnalogL_X, maxAnalogL_X, maxPWM, minPWM);
          }

          else if (valorAnalogicoEsquerdo < (centerAnalogL_X - toleranciaAnalogico)) {
            digitalWrite(SENTIDO_MOTOR_DIREITO, HIGH);
            digitalWrite(SENTIDO_MOTOR_ESQUERDO, LOW);
            pwmMotorDireito = map(valorAnalogicoEsquerdo, centerAnalogL_X, minAnalogL_X, maxPWM, minPWM);
            pwmMotorEsquerdo = map(valorAnalogicoEsquerdo, centerAnalogL_X, minAnalogL_X, minPWM, maxPWM);
          }

          else {
            digitalWrite(SENTIDO_MOTOR_ESQUERDO, LOW);
            digitalWrite(SENTIDO_MOTOR_DIREITO, LOW);
            pwmMotorDireito = 0;
            pwmMotorEsquerdo = 0;
          }
        }

        Serial.print("PWM Direito: ");
        Serial.println(pwmMotorDireito);
        Serial.print("PWM Esquerdo: ");
        Serial.println(pwmMotorEsquerdo);

        analogWrite(VELOCIDADE_MOTOR_DIREITO, pwmMotorDireito);
        analogWrite(VELOCIDADE_MOTOR_ESQUERDO, pwmMotorEsquerdo);
      }

      else
        desligaRobo();
    }
  }
}

void setup() {

  Serial.begin(115200);

  // Inicia comunicação Bluetooth que permite a conexão com controle.
  BP32.setup(&onConnectedController, &onDisconnectedController);
  BP32.enableVirtualDevice(false);

  // Desparea os controles que haviam sido conectados anteriormente.
  BP32.forgetBluetoothKeys();

  // Configura pinos da ESP32 para controle dos motores de arma.
  pinMode(PINO1_ARMA1, OUTPUT);
  pinMode(PINO2_ARMA1, OUTPUT);

  pinMode(PINO1_ARMA2, OUTPUT);
  pinMode(PINO2_ARMA2, OUTPUT);

  // Configura pinos da ESP32 para controle dos motores de locomoção.
  pinMode(SENTIDO_MOTOR_ESQUERDO, OUTPUT);
  pinMode(VELOCIDADE_MOTOR_ESQUERDO, OUTPUT);

  pinMode(SENTIDO_MOTOR_DIREITO, OUTPUT);
  pinMode(VELOCIDADE_MOTOR_DIREITO, OUTPUT);

  // Desliga movimentação e arma do robô.
  desligaRobo();
}

void loop() {
  // Checa se houve atualização nos dados do controle
  bool dataUpdated = BP32.update();

  // Se sim, chama a função processControllers() para processar os dados
  if (dataUpdated)
    processControllers();
}

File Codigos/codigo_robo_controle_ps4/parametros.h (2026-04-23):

#ifndef parametros_h
#define parametros_h

#include <Arduino.h>

#define PINO_LED_INTERNO 2

#define PINO_1_ARMA2 13
#define PINO_2_ARMA2 12

#define PINO_1_MOTOR_ESQUERDO 14
#define PINO_2_MOTOR_ESQUERDO 27

#define PINO_1_MOTOR_DIREITO 25
#define PINO_2_MOTOR_DIREITO 26

#define PINO_1_ARMA1 33
#define PINO_2_ARMA1 32

// Comportamento natural do controle em ambos os analógicos
// Cima + Baixo -
// Direita + Esquerda -

// Ambos os analógicos (E e D) tem o mesmo comportamento, retornam os mesmos valores para os mesmos sentidos / mesmas direções
// Ambas as direções retornam a mesma faixa de valores
// Os valores retornados para cada um dos sentidos em uma mesma direção (esquerda/direita ou cima/baixo) não são simétricos

const int32_t MIN_ANALOG_Y = -128, CENTER_ANALOG_Y = 0, MAX_ANALOG_Y = 127;
const int32_t MIN_ANALOG_X = -128, CENTER_ANALOG_X = 0, MAX_ANALOG_X = 127;

const int32_t TOLERANCIA_ANALOGICO = 3;  // zona morta do controle

// Pino de controle em HIGH: 255 (menor velocidade) a 0 (maior velocidade)
// Pino de controle em LOW: 0 (menor velocidade) a 255 (maior velocidade)

const int MIN_PWM = 0, MAX_PWM = 255;  // valores limite para o PWM da ESP32

#endif

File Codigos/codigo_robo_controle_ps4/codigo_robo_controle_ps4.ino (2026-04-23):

// Link para a biblioteca: https://github.com/aed3/PS4-esp32

#include <PS4Controller.h>
#include "parametros.h"

// Substituir o que está entre "" pelo endereço MAC salvo no controle
// Utilize a ferramenta sixaxispairer para descobrir o endereço
char* macAddress = "dc:97:ba:e7:d9:38";

bool roboLigado, configsTravadas;

/* Foi necessário utilizar essas variáveis para permitir a 
   inversão do sentido de giro de cada motor de locomoção */

int sentidoMotorEsquerdo, velocidadeMotorEsquerdo;
int sentidoMotorDireito, velocidadeMotorDireito;

bool direitoVesquerdoH, direitoHesquerdoV;

void desligaRobo() {
  analogWrite(sentidoMotorDireito, 0);
  analogWrite(velocidadeMotorDireito, 0);

  analogWrite(sentidoMotorEsquerdo, 0);
  analogWrite(velocidadeMotorEsquerdo, 0);

  roboLigado = false;
}

void processControllers() {

  if (PS4.Share()) {
    roboLigado = false;
    Serial.println("Robo desligado.");
  }

  else if (PS4.Options()) {
    roboLigado = true;
    Serial.println("Robo ligado.");
  }

  if (roboLigado) {

    /* --------------------- Lógica de funcionamento da arma --------------------- */

    // Se BOLINHA for pressionado, roda arma para um lado.
    if (PS4.Circle()) {
      Serial.print("Arma Sentido 1\n");
      analogWrite(PINO_1_ARMA1, 0);
      analogWrite(PINO_2_ARMA1, MAX_PWM);
      analogWrite(PINO_1_ARMA2, MAX_PWM);
      analogWrite(PINO_2_ARMA2, 0);
    }

    // Se QUADRADO for pressionado, roda arma para o outro lado.
    if (PS4.Square()) {
      Serial.print("Arma Sentido 2\n");
      analogWrite(PINO_1_ARMA1, MAX_PWM);
      analogWrite(PINO_2_ARMA1, 0);
      analogWrite(PINO_1_ARMA2, 0);
      analogWrite(PINO_2_ARMA2, MAX_PWM);
    }

    // Se TRIÂNGULO for presionado, desliga motores da arma.
    if (PS4.Triangle()) {
      Serial.print("Arma desligada\n");
      analogWrite(PINO_1_ARMA1, 0);
      analogWrite(PINO_2_ARMA1, 0);
      analogWrite(PINO_1_ARMA2, 0);
      analogWrite(PINO_2_ARMA2, 0);
    }

    /* ----------------- Lógica de trava das configurações ----------------- */

    if (PS4.L3() && PS4.R3()) {
      configsTravadas = !configsTravadas;
      digitalWrite(PINO_LED_INTERNO, configsTravadas);
      Serial.println(configsTravadas);
    }

    if (!configsTravadas) {  // Trava pra evitar de o público ficar alterando as configurações

      /* ----------------- Lógica de inversão dos analógicos de movimentação ----------------- */

      if (PS4.L1()) {
        direitoVesquerdoH = true, direitoHesquerdoV = false;
      }

      if (PS4.R1()) {
        direitoVesquerdoH = false, direitoHesquerdoV = true;
      }

      /* ----------------- Lógica de inversão de giro da movimentação ----------------- */

      if (PS4.Right()) {
        sentidoMotorEsquerdo = PINO_1_MOTOR_ESQUERDO, velocidadeMotorEsquerdo = PINO_2_MOTOR_ESQUERDO;
        sentidoMotorDireito = PINO_1_MOTOR_DIREITO, velocidadeMotorDireito = PINO_2_MOTOR_DIREITO;
      }

      if (PS4.Down()) {
        sentidoMotorEsquerdo = PINO_1_MOTOR_ESQUERDO, velocidadeMotorEsquerdo = PINO_2_MOTOR_ESQUERDO;
        sentidoMotorDireito = PINO_2_MOTOR_DIREITO, velocidadeMotorDireito = PINO_1_MOTOR_DIREITO;
      }

      if (PS4.Left()) {
        sentidoMotorEsquerdo = PINO_2_MOTOR_ESQUERDO, velocidadeMotorEsquerdo = PINO_1_MOTOR_ESQUERDO;
        sentidoMotorDireito = PINO_1_MOTOR_DIREITO, velocidadeMotorDireito = PINO_2_MOTOR_DIREITO;
      }

      if (PS4.Up()) {
        sentidoMotorEsquerdo = PINO_2_MOTOR_ESQUERDO, velocidadeMotorEsquerdo = PINO_1_MOTOR_ESQUERDO;
        sentidoMotorDireito = PINO_2_MOTOR_DIREITO, velocidadeMotorDireito = PINO_1_MOTOR_DIREITO;
      }
    }

    /* ----------------- Lógica de funcionamento da movimentação ----------------- */

    int8_t valorAnalogicoV, valorAnalogicoH;

    if (direitoVesquerdoH) {
      // Lê valor em Y do analógico direito (R-right).
      valorAnalogicoV = PS4.RStickY();

      // Lê valor em X do analógico esquerdo (L-left).
      valorAnalogicoH = PS4.LStickX();
    }

    if (direitoHesquerdoV) {
      // Lê valor em X do analógico direito (R-right).
      valorAnalogicoH = PS4.RStickX();

      // Lê valor em Y do analógico esquerdo (L-left).
      valorAnalogicoV = PS4.LStickY();
    }

    // Exibe valores no monitor serial.
    Serial.print("Y analogico: ");
    Serial.println(valorAnalogicoV);

    Serial.print("X analogico: ");
    Serial.println(valorAnalogicoH);

    int pwmMotorDireito1, pwmMotorDireito2, pwmMotorEsquerdo1, pwmMotorEsquerdo2;

    if (valorAnalogicoV > (CENTER_ANALOG_Y + TOLERANCIA_ANALOGICO)) {

      pwmMotorDireito1 = MAX_PWM;
      pwmMotorEsquerdo1 = MAX_PWM;

      if (valorAnalogicoH > (CENTER_ANALOG_X + TOLERANCIA_ANALOGICO)) {

        pwmMotorDireito2 = map(valorAnalogicoV - valorAnalogicoH,
                               CENTER_ANALOG_Y - MAX_ANALOG_X,
                               MAX_ANALOG_Y - CENTER_ANALOG_X,
                               MAX_PWM,
                               MIN_PWM);

        pwmMotorEsquerdo2 = map(valorAnalogicoV + valorAnalogicoH,
                                CENTER_ANALOG_Y + CENTER_ANALOG_X,
                                MAX_ANALOG_Y + MAX_ANALOG_X,
                                MAX_PWM,
                                MIN_PWM);
      }

      else if (valorAnalogicoH < (CENTER_ANALOG_X - TOLERANCIA_ANALOGICO)) {

        pwmMotorDireito2 = map(valorAnalogicoV - valorAnalogicoH,
                               CENTER_ANALOG_Y - CENTER_ANALOG_X,
                               MAX_ANALOG_Y - MIN_ANALOG_X,
                               MAX_PWM,
                               MIN_PWM);

        pwmMotorEsquerdo2 = map(valorAnalogicoV + valorAnalogicoH,
                                CENTER_ANALOG_Y + MIN_ANALOG_X,
                                MAX_ANALOG_Y + CENTER_ANALOG_X,
                                MAX_PWM,
                                MIN_PWM);
      }

      else {
        pwmMotorDireito2 = map(valorAnalogicoV, CENTER_ANALOG_Y, MAX_ANALOG_Y, MAX_PWM, MIN_PWM);
        pwmMotorEsquerdo2 = map(valorAnalogicoV, CENTER_ANALOG_Y, MAX_ANALOG_Y, MAX_PWM, MIN_PWM);
      }
    }

    else if (valorAnalogicoV < (CENTER_ANALOG_Y - TOLERANCIA_ANALOGICO)) {

      pwmMotorDireito1 = MIN_PWM;
      pwmMotorEsquerdo1 = MIN_PWM;

      if (valorAnalogicoH > (CENTER_ANALOG_X + TOLERANCIA_ANALOGICO)) {
        pwmMotorDireito2 = map(valorAnalogicoH + valorAnalogicoV,
                               CENTER_ANALOG_X + MIN_ANALOG_X,
                               MAX_ANALOG_X + CENTER_ANALOG_Y,
                               MIN_PWM,
                               MAX_PWM);

        pwmMotorEsquerdo2 = map(valorAnalogicoH - valorAnalogicoV,
                                CENTER_ANALOG_X - CENTER_ANALOG_Y,
                                MAX_ANALOG_X - MIN_ANALOG_Y,
                                MIN_PWM,
                                MAX_PWM);
      }
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

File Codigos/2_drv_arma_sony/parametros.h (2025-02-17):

#ifndef parametros_h
#define parametros_h

#include <Arduino.h>

#define PINO1_ARMA2 13
#define PINO2_ARMA2 12

#define SENTIDO_MOTOR_ESQUERDO 14
#define VELOCIDADE_MOTOR_ESQUERDO 27

#define SENTIDO_MOTOR_DIREITO 25
#define VELOCIDADE_MOTOR_DIREITO 26

#define PINO1_ARMA1 33
#define PINO2_ARMA1 32

// Comportamento natural do controle em ambos os analógicos
// Cima - Baixo +
// Direita + Esquerda -

const int32_t minAnalogR_Y = -512, centerAnalogR_Y = -4, maxAnalogR_Y = 508;  // Valores reais * -1
const int32_t minAnalogL_X = -508, centerAnalogL_X = 4, maxAnalogL_X = 512;

const int32_t toleranciaAnalogico = 10;  // zona morta do controle

// Pino de controle em HIGH: 255 (menor velocidade) a 0 (maior velocidade)
// Pino de controle em LOW: 0 (menor velocidade) a 255 (maior velocidade)

const int minPWM = 0, maxPWM = 200;  // valores limite para o PWM da ESP32

#endif

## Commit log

2024-06-04 sserial.print editado
2024-06-04 pinos motores organizado
2024-06-04 arquivos DXF robos
    [Arma.dxf, Arma1.dxf, Arma2.dxf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]
2024-06-18 furos abracadeira + arma nova
    [Arma3.dxf, Base.dxf, Frente - Part 1.dxf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]
2024-06-21 codigos especificos para os controles
2024-07-25 tutoriais para iniciativa
2024-07-26 fotos carcacas adicionadas
    [Arma.dxf, Base.dxf, Frente - Part 1.dxf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]
2024-07-26 tutoriais upload, arduino e driver
2024-08-23 codigo 2 motores arma
2024-08-25 organizado + tutorial arma motor
2024-12-03 codigos 2 motores arma
2024-12-03 alteracao pinagem + limitacao vel. motor arma
2025-01-30 novo robo 1
    [Arma.dxf, Base.dxf, Frente - Part 1.dxf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]
2025-01-31 alteracao carcaca
    [topo1.dxf, topo2.dxf]
2025-02-10 carcaca robo 1 2025
    [Arma.dxf, Base.dxf, Traseira.dxf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]
2025-02-10 carcaca robo 2 2025
    [Arma.dxf, Base.dxf, Lateral 1.dxf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]
2025-02-10 torre do motor
    [torre1.dxf, torre2.dxf]
2025-02-17 vaos arma aumentados, vaos encaixes aumentados, cantos torre arredondados, furo traseiro base removido e dentes frente modificados
    [Base.dxf, frente.dxf, lateral1.dxf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]
2025-02-17 nome pinos modificados e valor max saida PWM reduzido
2025-02-17 numerro / nome pinos modificados e valor max saida PWM reduzido
2025-02-17 logica inversao arma add, troca digital para analog pinos arma, troca teclas acionamento arma
2025-02-18 bordas arredondadas e furo motor movido para frente pra arma não pegar na carcaca
    [torre.dxf]
2025-02-18 recortes diminuidos pras peças encaixarem firme
    [Base.dxf, topo1.dxf, topo2.dxf]
2025-02-18 suportes e laterais novas descartados, furos desnecessarios removidos vao conector arma aumentado
    [Base.dxf, Traseira.dxf, lateral1.dxf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]
2025-02-24 furos removidos
    [lateral1.dxf, lateral2.dxf]
2025-02-24 filete e furo fio motor diminuidos
    [Base.dxf, torre.dxf]
2025-02-24 furo removido
    [lateral1.dxf, lateral2.dxf]
2025-02-24 frente pra não deixar a placa cair do robo
    [Base.dxf, frente.dxf]
2025-02-24 furo na base para fixar traseira
    [Base.dxf]
2025-02-24 espacamento entre suportes arma modificado
    [Base.dxf, frente.dxf, topo1.dxf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]
2025-02-28 roda em mdf - 17g mais leve que a amarela
    [extensor.dxf, roda.dxf]
2025-03-14 logica pinos movimentacao no loop + funcao de inverter motores locomocao isoladamente
2026-01-23 ajustes na carcaca
    [apoio_torre.dxf, frente.dxf, lateral1.dxf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]
2026-01-23 armas modificadas + novos modelos
    [arma_curva.dxf, arma_martelo.dxf, arma_meia_curva.dxf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]
2026-01-23 trava de config motores adicionada
2026-04-23 arquivos atualizados
    [base.dxf, eixo_arma_3d.stl, eixo_hub_3d_1.stl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]
2026-04-24 imagens para montagem
